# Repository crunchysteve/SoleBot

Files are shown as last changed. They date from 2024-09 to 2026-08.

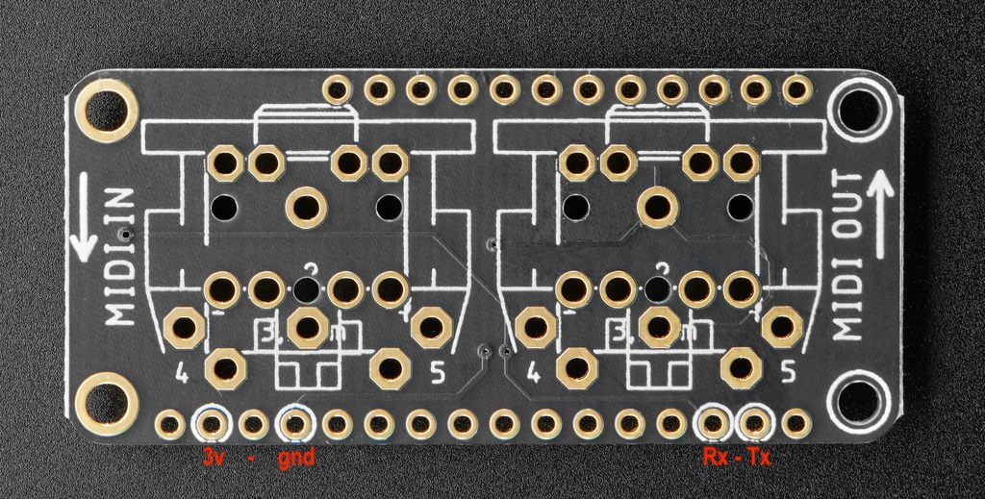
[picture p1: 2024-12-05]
images/adafruit_products_MIDI_FW_pinouts_bottom.jpg

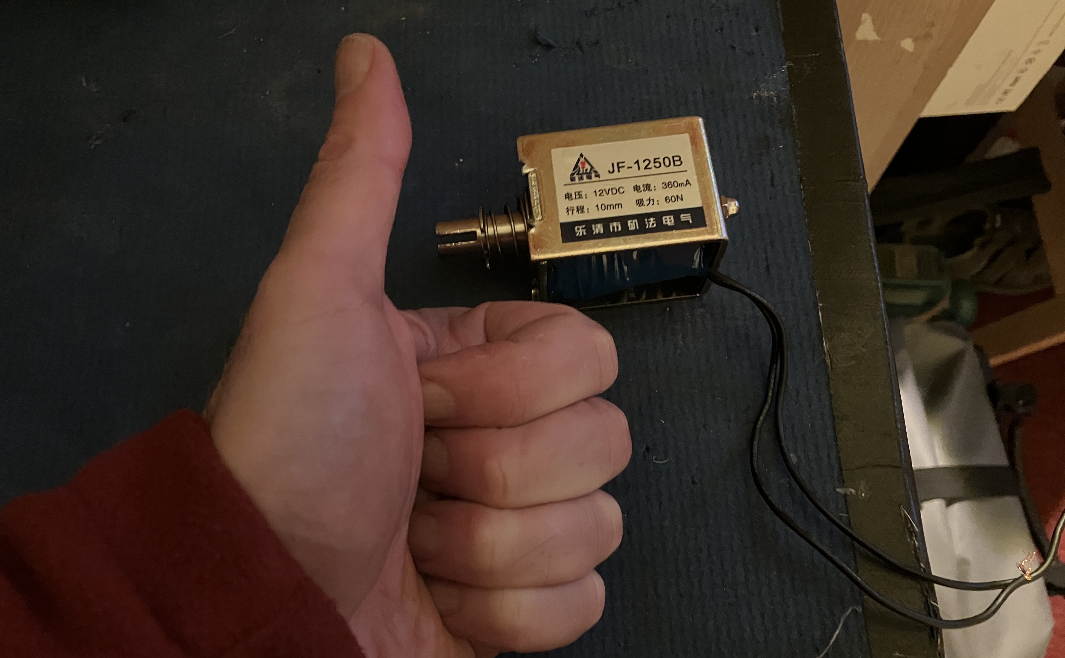
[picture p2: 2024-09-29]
images/cymbalLifterSolenoid.jpg

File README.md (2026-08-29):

# Announcement

Where did Solébot go? It has gone to [Codberg.org](https://codeberg.org/crunchysteve/SoleBot), as have most of my other repos, although a few have been deleted.

Why? After experiementing with the hyperscale AIs and finding them pretty much useless, then, seeing a very dear friend let his brains fall out by using AI how he should do anything in his life, all the while admitting his own laziness. The enshittification brought about by AI doing the work of humans or humans using AI to do work they're not qualified to do, I'm cutting AI out of my life in the ways I have control over and, where it might be useful, only running small, local hosted models on hardware I own and can isolate.

Part of this was turning off CoPilot here, only to find that, while it's tuned of when I'm coding, CoPilot still intrudes at my commit info. Of all the things I've never needed AI for, commits are one of them. I'm a hobbyist, not a professional. I'm a socialist, not a capitalist. My commit info is for me and none of it needs tracking and I Never needed a CoPilot co-writer for the commits I was making, and mostly don't need a traceable workflow. Arduino code is pretty simple stuff.

For me, Github was, before Microsoft bought it, a place to store my code that had a cool history. Using Github felt like beng distantly associate with Linus.

Since Microsoft took over, wheedling CoPilot insistently into my face, more annoying than Clippy ever was, finally refusing to allow me to even write my commits in peace, even though I turned it off everywhere I was allowed to - Time to quit Github. One repo at a time, staring with Solebot, because it's the most important coding project in my small existence.

When the AI comes for Nadella's job, either literally, or as Microsoft does a 10-10-10 score swan dive on the NASDAQ, I'll be quietly hobby coding over at a repo that has sensible AI policies and more of a small coder spirit.

Cheers,
Crunchy.

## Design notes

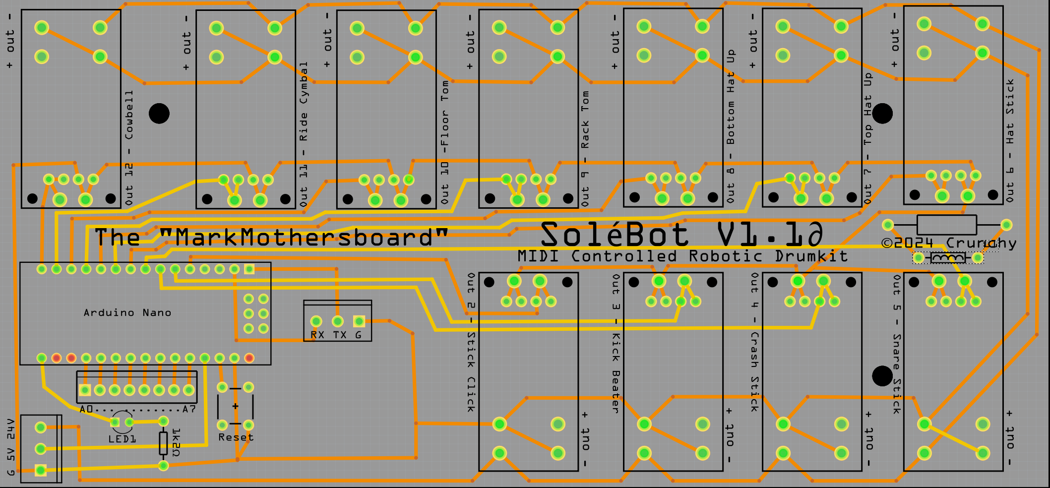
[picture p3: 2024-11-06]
images/SoleBotPCBV1.1∂_pcb.png

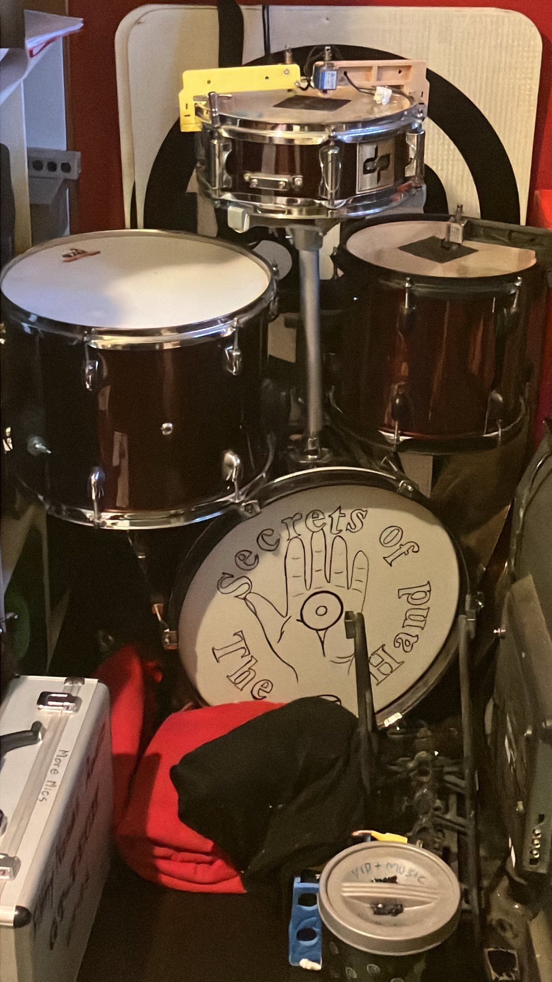
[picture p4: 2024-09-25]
images/drumset.jpg

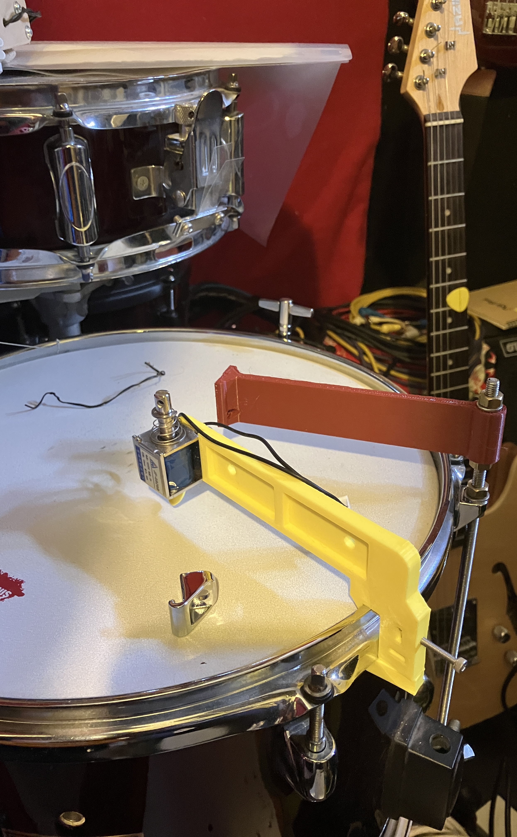
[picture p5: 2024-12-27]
images/newDrumBeaterBrktWithHoopClip.jpeg

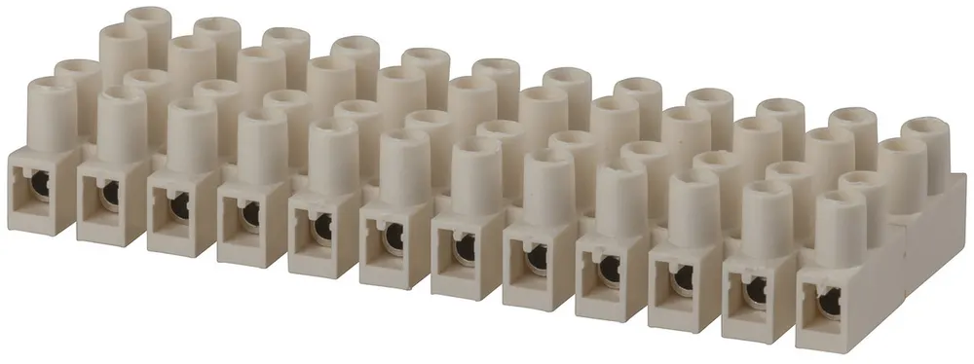
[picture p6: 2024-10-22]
images/HM3202_plug-socket-12-way-screw-terminal-strip_82612.png

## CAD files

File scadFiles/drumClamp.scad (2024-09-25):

/*
  MIDI Driven Drumbot
  ©2024 Crunchysteve
  ----------------------
  This code will be the MIDI driven heart of SoléBot, the solenoid driven drumbot. 

  Dynamics are provided by using analogWrite() on channels that need them, or digitalWrite() for 
  the channels that don't, with a timed pulse to kick 12v solenoids with 24v for just long enough 
  to never exceed 24W RMS applied to each solenoid, even at maximum tempo. The MIDI note number 
  corresponding to each drum will determine which solenoid operates, while MIDI velocity + 127 
  applied to analogWrite() on the PWM outputs will generate soft to loud hits.

  This code will run on almost any micro, but the pins are setup for an Arduino Uno or Nano. 
  Use a dual AOD4184 MOSFET module, such as this one, 
    https://core-electronics.com.au/mosfet-power-switch-module.html, to drive each solenoid.

  I'm using JF-0826B 12v/2A 20N solenoids and, because of the light duty cycle, I run them from
  24V via the MOSFET boards. I haven't tried higher than 30v yet, but neither Solenoids nor the 
  MOSFETS run hot at 30v, even when run for extended periods. Non-blocking timing will be used to 
  pulse PWM drive just long enough to get the beater within a millimetre of the drum skin.
  
  All code, including C code and the OpenSCAD bracket 3D files, are hosted on
    https://github.com/crunchysteve/Solebot while,
  the OpenSCAD models are also hosted here 
    https://www.thingiverse.com/thing:6771931 without without C code.
  
  This code is copyright ©2024 Crunchysteve and is available for use or modification under an MIT 
  licence, except for commercial use, whereupon the author would appreciate a percentage of device 
  sales in exchange for any licence for manufacturing this project commercially.

  This preamble must always remain at the head of all 3d models and source code.
*/

use <solenoid.scad>
use <beaters.scad>

arm();
//translate([0,17,4]) snareSolenoid();

module arm(){
    translate([0,17]) difference(){
        linear_extrude(height=12) difference(){
            offset(6) offset(-6)square([140,27]);
            translate([17,20.5]) circle(2);
            translate([5,6]) circle(2);
            for(x=[65,115]) for(y=[6.5,20]) 
                    translate([x,y]) circle(1.5);
        }
        translate([-1,-1,4]) cube([23,29,9]);
        for(x=[27,77]) translate([x,4,4]) cube([45,19,9]);
    }
    difference(){
        union(){
            translate([114,1,0]) cube([6,17,12]);
            translate([120,8,0]) cube([10,12,12]);
            translate([129,-16,0]) cube([17,40,12]);
            translate([122,-25,0]) cube([5,12,12]);
            translate([124,-25,0]) cube([22,8,12]);
        }
        translate([113,1,4]) 
                rotate([0,0,45]) cube([9,9,146],center=true);
        translate([121,4,6]) rotate([0,90,0]) cylinder(r=1.7,h=40);
        translate([138,4,6]) cube([3,8,16],center=true);
        translate([138,-26,6]) rotate([-90,0,0]) cylinder(r=1.7,h=40);
        translate([138,-7,6]) cube([8,3,16],center=true);
        translate([146,24,6]) 
                rotate([0,0,45]) cube([9,9,146],center=true);
    }
}

module snareSolenoid(state=false) translate([0,0,25]) rotate([-90,0,0]){
    value = state ? -11 : -4;
    solenoid();
    translate([11,12.5,value]) mirror([0,0,1]) rotate([0,-10,0]) stickTip();
}

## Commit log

2024-08-29 Sorted, ready for 3D code uploads.
    Arduino/PlatformIO code coming soon. Gotta re-breadboard everything. New, simpler, mosfet drive modules to be tested.
2024-08-29 Add 3D models for printable parts.
    Initial model commits.
    [KickRiser.scad, KickRiser.stl, beaters.scad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]
2024-08-29 Update README.md to include Pulsed PWM simulation.
2024-09-13 Project status update.
    Black Friday September 2024 project status update. I'm pretty confident now that using solenoids rather than car door lock motors is the go.
2024-09-19 First simple test program - initial commit
    A simple, repetitive testprogram to prove that the solenoid hits the drum and sounds like a stick hit.
2024-09-19 Video of the basic operation
    Video of the solenoid on a test rig then one of the right side of the actual snare drum assembly being operated by the simple test program.
2024-09-20 Update testTool.ino
    Expand the test pattern to operate multiple solenoids. MIDI version coming soon.
2024-09-23 Add aluminium solenoid bracket design.
    [drumBracket.scad]
2024-09-25 Make project Arduino IDE compliant by unifying folder and file namesakes.
2024-09-25 Include serial MIDI Arduino library
2024-09-25 Add rights preamble to 3D files
    [KickRiser.scad, beaters.scad, drumBracket.scad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]
2024-09-27 Create early draft of MIDI driven SoléBot code for Uno or Nano
    [snareClamp.scad]
2024-09-27 Add short LED flashes for drum hits, offs and timeouts.
2024-09-27 remove defunct OpenSCAD file
    [snareClamp.scad]
2024-09-27 Change name of KickRiser.scad to kickRiser.scad
    [KickRiser.scad]
2024-09-27 Update README.md by removing now irrelevant previous material.
2024-09-29 Added image and detail to printed parts list and CAD "vitamins" in README.md
2024-09-30 Add Preliminary control board for Nano and 11 MOSFET switch modules. (4 piece kit)
    [SoleBotPCBV1.0∂.fzz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]
2024-09-30 Update README.md with PCB announcement
2024-09-30 Repair error in printed circuit board
    [SoleBotPCBV1.0∂.fzz]
2024-09-30 Add JF-1250B solenoid model to solenoids.scad
    [solenoids.scad]
2024-09-30 Add demonstrations to solenoids.scad
    [solenoids.scad]
2024-09-30 Note the new solenoid in PARSTLIST.md
2024-10-02 Many updates
    [SoleBotPCBV1.0∂.fzz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]
2024-10-02 update PCB
    [SoleBotPCBV1.0∂.fzz]
2024-10-02 Fix 2 circuit board errors in Fritzing and Gerber files
    [SoleBotPCBV1.0∂.fzz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]
2024-10-02 PCB ready
    [SoleBotPCBV1.0∂.fzz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]
2024-10-02 HiHat design preliminary prototype video.
2024-10-21 Adding Control Board Explainer
    [SoleBotPCBV1.0∂.fzz]
2024-10-22 Expand on power control in controlBoard.md
2024-10-22 Add link to example mosfet board seller
2024-11-01 MarkMothersboard PCB repairs (Fritzing & Gerber)
    [SoleBotPCBV1.0∂.fzz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]
2024-11-03 Breaking News: The electronics are tested and working, the Fritzing PCB file has been improved.
2024-11-06 More errors fixed in PCB files
    [SoleBotPCBV1.0∂.fzz, SoleBotPCBV1.1∂.fzz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]
2024-11-07 Added KiCAD file (Converted from Fritzing via Gerber Viewer, may be useless.)
2024-11-24 put serial pin IDs in pins.h
2024-11-26 Rewrite to use switch/case rather than for-loop for striking beats.
2024-12-05 Add Adafruit MIDI Feather Wing to PARTSLIST.md
2024-12-05 Fix Feather Wing image link
2024-12-05 Add Adafruit Feather Wing Kit to PARTSLIST.md
2024-12-12 Update README.md with news of progress building the prototype
2024-12-17 Add a new style drum solenoid mounting bracket design for use with M6/1/4" threaded rod and Gibratar Vintage Rim Clamps.
    [GibraltarVintageRimClampBracket.scad, GibraltarVintageRimClampBracket.stl, NewHatMech.scad]
2024-12-18 Tweak new solenoid bracket
    [GibraltarVintageRimClampBracket.scad, GibraltarVintageRimClampBracketForJF0826BSolenoid.stl, threadedRod.scad]
2024-12-18 Some messy scad file changes, sorry.
    [GibraltarVintageRimClampBracket.scad, GibraltarVintageRimClampBracket.stl, GibraltarVintageRimClampBracketForJF0826BSolenoid.stl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]
2024-12-27 Add and sync new bracket pictures in README.md
2024-12-27 Update README.md with new bracket images.
2024-12-27 Change older solenoid brackets to [DEPRECATED]
    [drumClamp_DEPRECATED.scad]
2024-12-27 Add link in README.md to off-the-shelf bracket component from Gibraltar Hardware.
2024-12-29 Update new solenoids brackets. (Still more work to do, tho')
    [GibraltarVintageRimClampBracket.scad, KickRiser.scad, drumClamp_DEPRECATED.scad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]
2024-12-29 Temporary link to deprecated scadfile and STL file for kickRiser.
    [KickRiser.scad, KickRiser.stl]
2024-12-31 Withdraw incomplete mechanism from SCAD files
    [NewHatMech.scad]
2025-02-02 Begin adding parts for modoified hi-hat stand.
    [hatStandOpenerBrkt.stl, hatstand.scad]
2025-02-02 update includes in drumBracket.scad
    [drumBracket.scad]
2025-02-14 zip gerber file and delete gerber folder
    [hatstand.scad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]
2025-11-21 Update README.md
    News note about why the project is currently not progressing.
